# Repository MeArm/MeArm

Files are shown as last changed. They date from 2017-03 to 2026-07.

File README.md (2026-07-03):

MeArm - Pocket Sized Robot Arm 
===========================

4503_additional-mearm-raspberry-pi-transparent-blue-robot-arm_11993340-8186-438d-b66b-95b7427ab5bc_800x

The MeArm is a small robot arm, designed make robotics and coding available at low cost. The project has been hugely successful in its objectives, due to the massive number of clones that have been made and sold across the world. There isn't an online market place where you can't buy a copy of this project. We continue to support the product through income made from the sale of high quality robot kits, manufactured and shipped from the UK.

[MeArm Website](https://www.mearm.com/) Where kits are available to purchase.

[MeArm GitHub](https://github.com/MeArm) Code and resources.

[phenoptix Thingiverse](https://www.thingiverse.com/phenoptix/designs) Physical designs and dxf files, alternative hosting, and other designed products.

Controllers and firmware for the MeArm are available for many different platforms, and can all be found in our [company github](https://github.com/MeArm).

## Available Controllers

Arduino
  - [Library with Inverse Kinematics](https://github.com/MeArm/MeArm-Arduino)
  - pcb V1.0 - AKA Brains Board using Pro Mini Clone
  - pcb V2.0 - AKA MeArm Wifi using ESP8266

Raspberry Pi
  - [node.js control](https://github.com/MeArm/mearm-js)
  - pcb V1.0 MeArm Pi

micro:bit 
  - [pxt adds blocks to makecode](https://github.com/MeArm/pxt-microbit-mearm)
  - [makecode hosted on microbit.org](https://makecode.microbit.org/22476-86653-83739-82174)
  - pcb all versions AKA MeArm micro:bit 

BeagleBoneBlack -[ Software hosted by Bob Stone](https://github.com/RorschachUK/meArmBBB)

Espruino - [JS Hardware with MeArm Examples](https://www.espruino.com/MeArm)

SparkCore - [Software with features such as S-Curve movements
](https://github.com/Hack-a-Day/Spark-MeArm)

Repository Contents
-------------------
This repository contains the design and cutting files for the MeArm. The MeArm is an Open Source 4DOF robot arm. It is intended to be a low cost and accessible robotics project for STEAM education.

Laser cut (3mm) dxf files and Assembly instruction pdf files are sorted into folders based on versions.

Files are collected from the various sources listed above.

## Watch the Build Video on YouTube

<a href="https://www.youtube.com/watch?v=eFOgFglWql4">youtube-thumb</a>

Version History
---------------

Available in this repository

* V3.0 Revised with no elastic bands, still requires a PCB. Build time around 40 minutes.
* V2.0 Designed for MeArm Pi Kickstarter, incorporates a PCB in the base. Requires elastic bands or nitrile O rings. Build time 30 minutes.
* V1.0 First finished version. No PCB required. Build time around 2 hours.

All hosted on Thingiverse .

* V1.0 ([First Finished Version](http://www.thingiverse.com/thing:993759))
* V0.4 ([Considered the Beta Arm](http://www.thingiverse.com/thing:360108))
* V0.3 ([Considered the Alpha Arm](http://www.thingiverse.com/thing:298820))
* V0.2 ([Heavy Weight Revision](http://www.thingiverse.com/thing:293707))
* V0.1 ([Proof of Concept](http://www.thingiverse.com/thing:257990))

License Information
-------------------
The hardware is released under [Creative Commons Share-alike 3.0](http://creativecommons.org/licenses/by-sa/3.0/).  
All other code is open source so please feel free to do anything you want with it; you buy me a beer if you use this and we meet someday ([Beerware license](http://en.wikipedia.org/wiki/Beerware)).
Also this boiler plate is yoinked from Sparkfun with thanks. Images are CC-SA-NC soz, have the files and design but take your own pics ;)

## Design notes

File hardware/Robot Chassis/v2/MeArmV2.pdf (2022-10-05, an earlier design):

Place the base PCB face up (the word TOP should be up) then insert the servo with the double ended arm (there's only one of these) into the hole in the centre. It needs to go the right way around so align the servo arm with the circle on the board

## Read this first!

The MeArm is designed to be easily built with a hex key and some enthusiasm. Here are some tips for a successful build:
Don’t overtighten! The
joints should move freely. If there’s any friction then
loosen off the screws.
Don’t force parts! If a part doesn’t seem to fit, don’t force it, it might just need to be flipped around.

For more detailed video
instructions visit:
http://learn.mime.co.uk/mearm

Slide the centre piece (part #1) down over the servo. The tabs are sized so it will only go on one way round. Wind the servo cable around the centre piece in a clockwise direction through the two holes and then plug it in to the pins as shown

Slide the end pieces (parts #2) down over the centre piece so that they slot into the base. Again, these will only go on one way around

Slide the left side (part #3) over the pins in the base

Slide the right side
(part #4) over the
pins in the base. Loop
one of the elastic
bands around the base
in the upper set of
slots in the sides.
Put this assembly to
one side

Slide the
crossbrace (part
#10) into the left

main strut (part
#5) and click it

in to place

Attach the left rear
strut (part #7) to
the rear of the long
strut you just added
using a 6m screw. It
should go on the
same side as the
main strut

Put the two short
lower levers (parts #8
and #9) together so
that the larger hole
is facing to the
outside, then attach
this to the rear strut
you just added using a
10mm screw through the
hole at the thin end

Clip on the right main
strut (part #11) to the
crossbrace

Screw the rear
strut to the
base using a 6mm
screw

#1

Take the base you
previously built and
screw the arm piece on to
the centre piece of the
base using a 6mm screw.
The screw should go
through the lower lever
and screw into the centre
piece of the base

Slide the right servo in
to place so the servo
arm slots into the hole.
Attach a servo clip
(part #14) to either
side of the servo and
clip it in to the bottom
of the base. Wind the
cable anticlockwise
around the servo clips
and then plug it into
the pins on the base
with the yellow wire to
the right

Slide the right servo in to place and clip it on in the same way. Wind the cable
anticlockwise around the servo clips and then plug it into the pins on the base with the yellow wire to the right.
Place an elastic band around the base and servo clips.

Attach the long strut
(part #6) to the top
of the previous part
using a 10mm screw.
The screw should go
through and hold the
crossbrace in place

# Instructions

#1 | #2 | #3 | #4

Put a 10mm
screw through the
thicker end of part #13
and then through the
triangular piece (part
#12). This piece should

be aligned so that the
screw goes through the
hole marked with a small
triangle and the “m” is
upright

Attach the
upper strut (part
#7) to the upper hole

of the triangular piece
using a 6mm screw

Attach the
right rear strut
(part #7) to the rear
hole on the triangular
piece using a 6mm screw

Put this assembly to one side for a moment

# Continue on the other side >

#5 | #6 | #7 | #8

#9 | #10 | #11 | #12 | #13

#14 | #15 | #16 | #17

MeArm Pi Instructions | MeArm WiFi Instructions

# MeArm Maker Instructions

Take the remaining servo and align the arm as shown in the picture. Take the left grip side (part #15) and slide it on to the end of the servo closest to the arm

Slot the centre grip support (part #16) on to the other end of the servo facing the same way as the other end

Clip the grip front plate (part #17) on to the front of the two pieces you slotted on to the servo. It should clip up into place. Make sure the extra hole is at the opposite end to the servo arm

Slot the left grip side (part #18) in to the third hole in the front plate

Slide the rear grip support (part #19) in to the gap and turn it up so it slots into place. The lower edge of it should be level with the front plate

Take the left grip (part #20) and place it over the servo arm. Align the right grip (part #21) with the left and hold in place

#26a Align the two

large base pieces
as shown. Screw
them together
using four 6mm
screws. Do not
overtighten the
screws

#26b Stretch the

elastic bands
over the sides of
the base to use
as feet

Gently prise the two base plates apart and slide the servo arm in between them and slide it down the central slot until it clips into place in the hole in the bottom

Slide the grip base
(part #22) on so
that the large hole
aligns with the
servo arm side and
screw it into place
through the right
grip with a 10mm
screw

Before starting this part set up your SD card. Instructions at: http://learn.mime.co.uk/mearm

Attach the grip to the rest of the arm using three 6mm screws. Tuck the cable down through the slot on the grip, then in and out of the
crossbrace on the arm,
plugging it in to the pins on the base with the yellow wire on the right.
Now choose one of the
following three steps to
continue

Attach the final
elastic band across
the front of the
base to hold the
plates together and
make a stable foot
to stand it on

Plug the two parts
together using the
ribbon cable provided

## Congratulations!

You’ve just built a robot arm!

Plug in the power supply to get it working and visit: http://learn.mime.co.uk/mearm
to begin using and programming your MeArm

If you have any problems you can get help at: http://mime.co.uk/support

#26a Align the two

large base pieces as
shown. Plug the HAT
on to the GPIO pins
of the Raspberry Pi.
One by one, slot a
spacer in between the
Pi and HAT then slot a
16mm screw through to hold it in place. Screw all four screws into the holes in the base

#26a Align the two

large base pieces
as shown. Slot the
small round spacers
under the PCB then
screw in a 10mm screw
to hold it in place

Do not overtighten the screws

#26c Fit the cover

over the tabs on the
sides and stretch an
elastic band over each
side. Push the joystick
caps on to the joysticks,
making sure they are properly aligned before pushing

#26c Fit the

cover over the
tabs on the sides
and stretch an
elastic band over
each side. Push the
joystick caps on to the
joysticks, making sure they are properly aligned before pushing

#26b Slot the front (part #24) and back (part #23 or #25

for the Pi Zero) edges
into place. Slot part
#25 into place on the

left of the base plus
one on the right if
you're using a Pi Zero

#26b Slot the front (part

#24) and back (part #23)

edges into place. Slot
parts #25 into
place on the
right and left of
the base
#18 | #19 | #20 | #21 | #22 | #23

#24 | #25

#27 | #29

#28

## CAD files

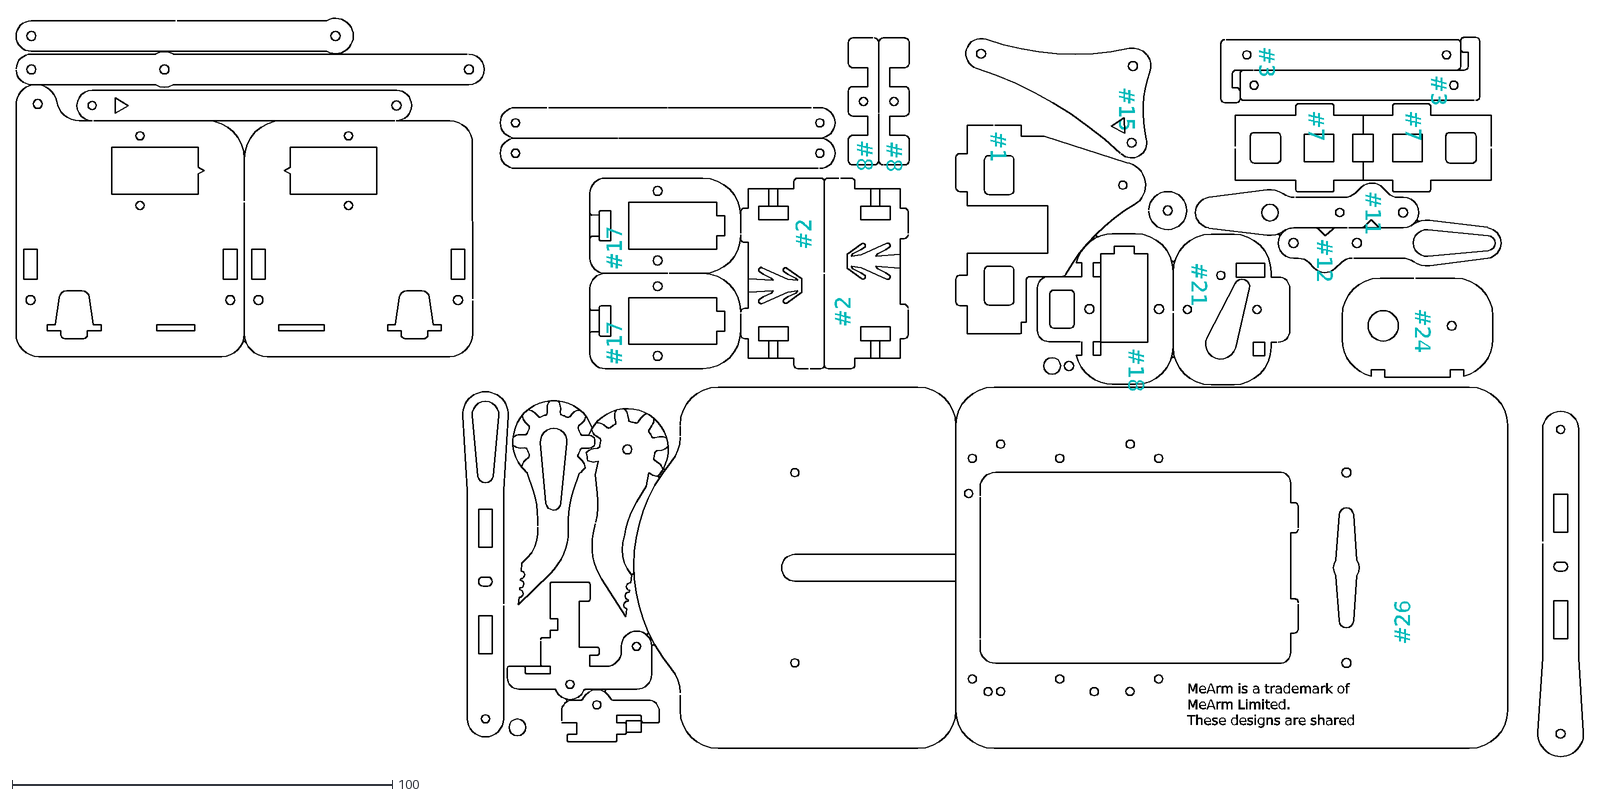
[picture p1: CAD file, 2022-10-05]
hardware/Robot Chassis/v3/MeArmV3.dxf
#26
#1
#3
#7
#8
#11
#12
#15
#18
#21
#24
#2
#17
MeArm is a trademark of
MeArm Limited.
These designs are shared

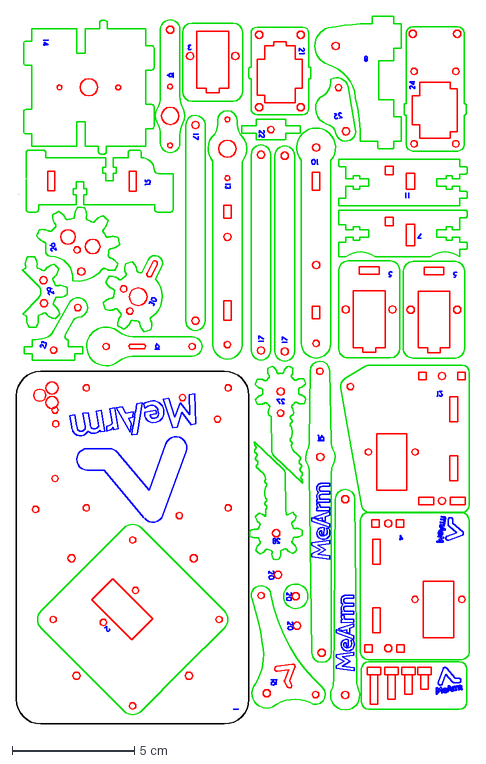
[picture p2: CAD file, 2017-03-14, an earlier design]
hardware/Robot Chassis/v1/MeArmV1.1.dxf
18.5 x 28.9 cm

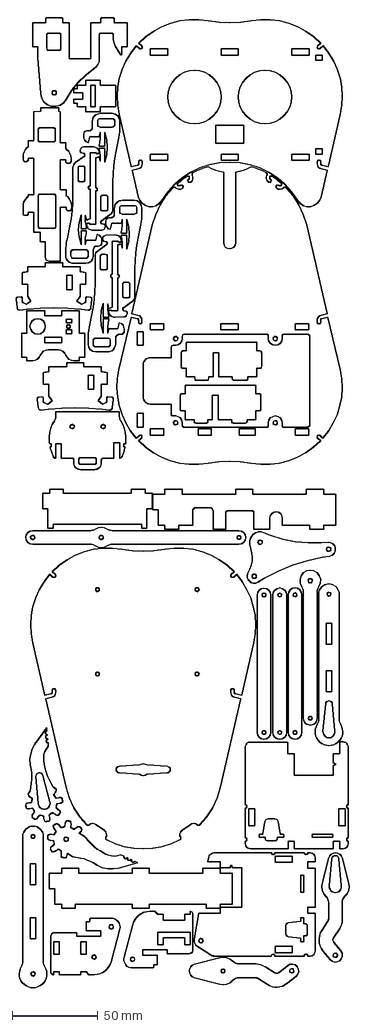
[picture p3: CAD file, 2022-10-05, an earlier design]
hardware/Robot Chassis/v2/MeArmV2.dxf
194.2 x 565.6 mm

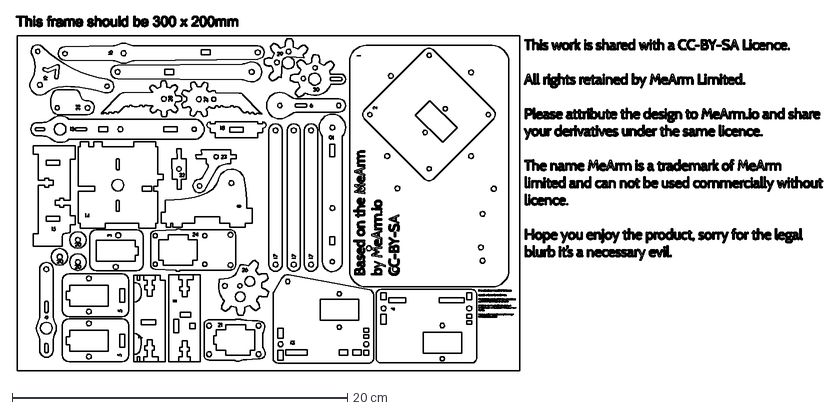
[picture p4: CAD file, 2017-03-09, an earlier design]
hardware/Robot Chassis/v1/MeArmV1.0.dxf
48.1 x 21.2 cm

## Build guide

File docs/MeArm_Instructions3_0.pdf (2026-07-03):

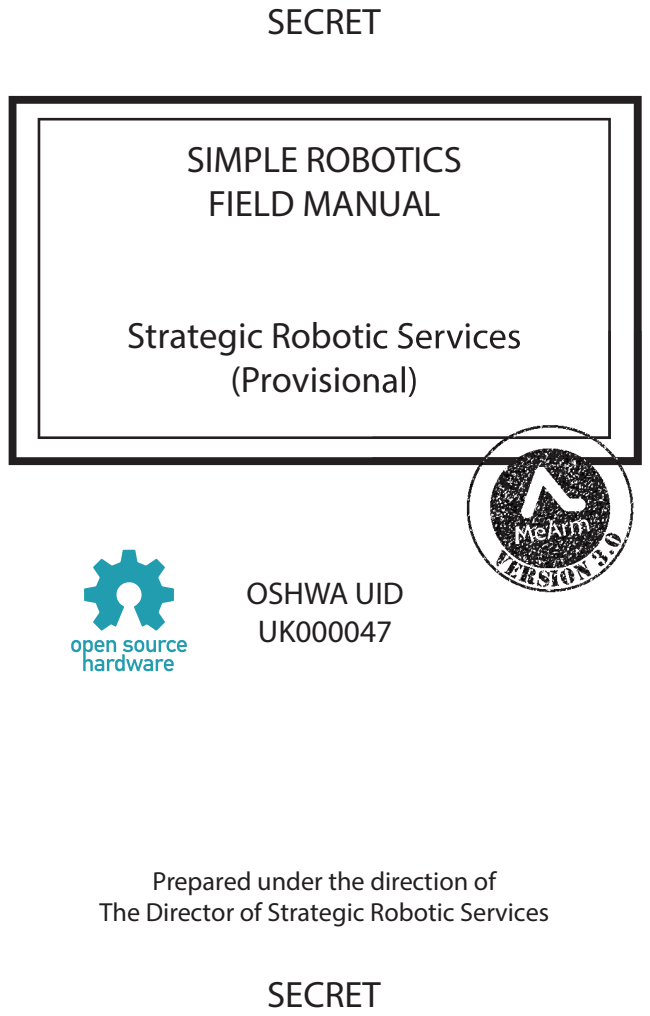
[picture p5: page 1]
SIMPLE ROBOTICS FIELD MANUAL; SECRET; OSHWA UID UK000047

Strategic Robotic Services
(Provisional)

Prepared under the direction of
The Director of Strategic Robotic Services

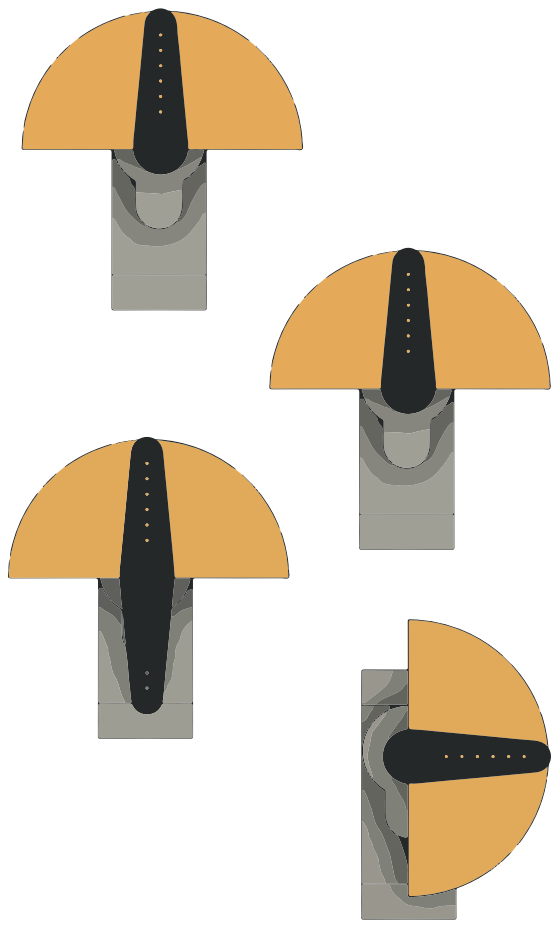
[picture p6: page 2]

Important Notes:

Before assembly you will need to test and calibrate your servo motors to the positions shown overleaf.

The process differs depending on your choice of control board. Please head to https://shop.mearm.com/build and select the correct product.

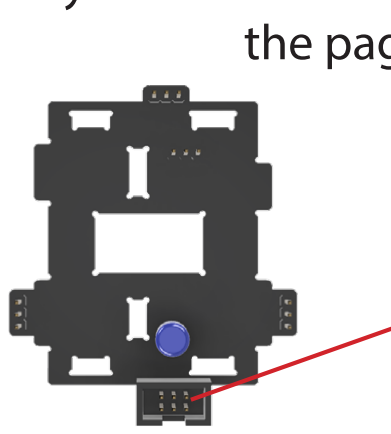
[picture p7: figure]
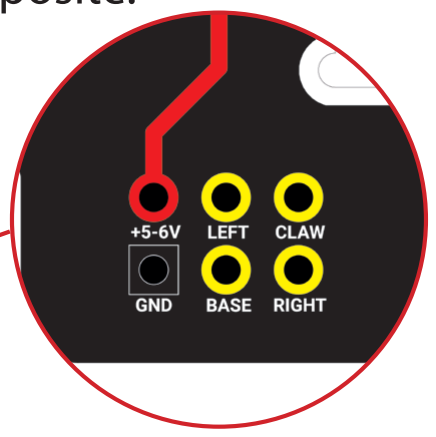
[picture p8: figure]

If you do not calibrate your servo motors now you will need to dismantle parts of your MeArm later on.

Do not skip ahead. Calibrate your servos so they are able to move in the arcs shown on the page opposite.

The MeArm project started in 2014, with the aim of making a robot arm that was made from a small number of components, was easy to assemble, and fun to use. The design files were shared online and the first viral robot arm was born. This latest version is the product of thousands of hours of open source development, from all around the globe.

We hope you will enjoy the product you have purchased, and we thank you for your support and feedback.

Remember:
- Joints should move freely. Without the servo motors fitted the robot should be a like a resting marionette.
- Parts should sit in place with very little or no force. It may be that you can rotate a part to get it to fit.

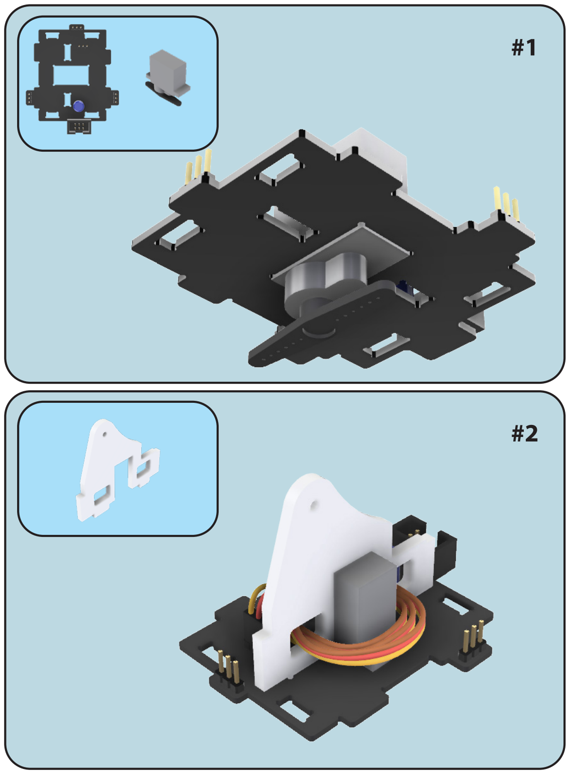
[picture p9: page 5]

#1

#2

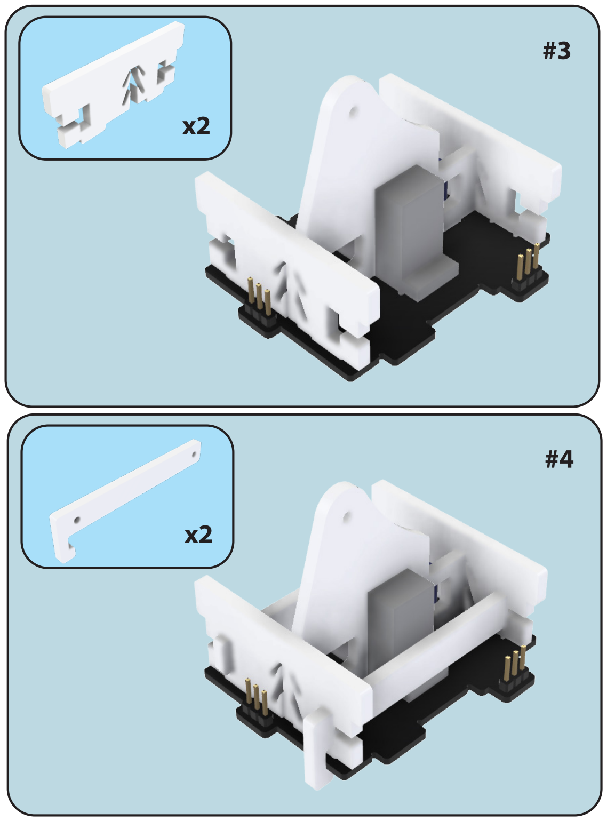
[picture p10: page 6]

#3

x2

#4

x2

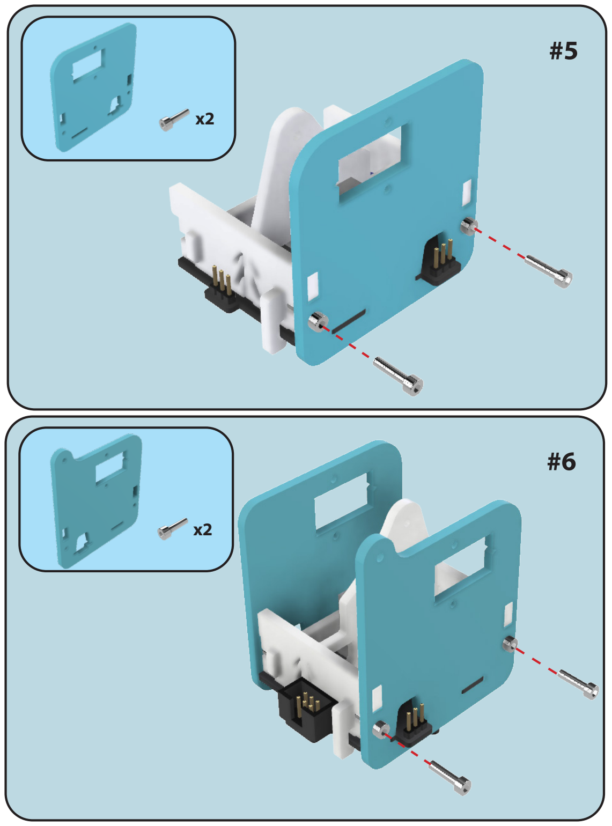
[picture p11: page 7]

#5

x2

#6

x2

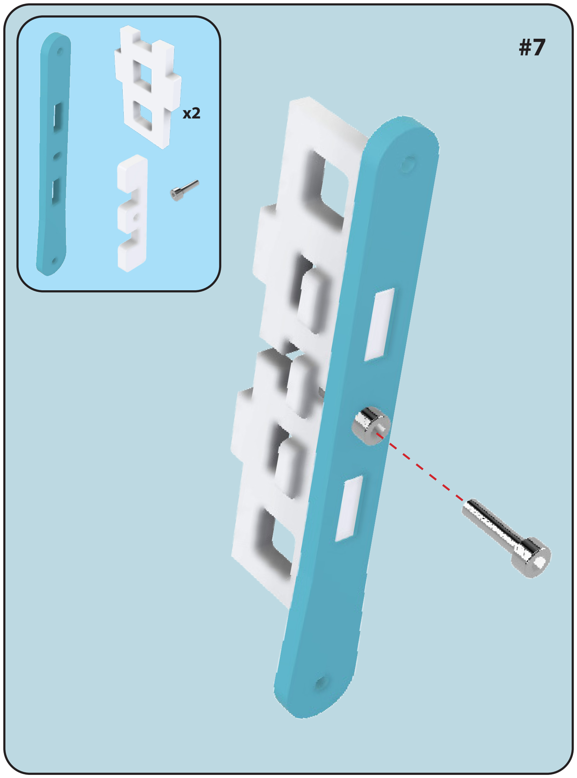
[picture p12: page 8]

#7

x2

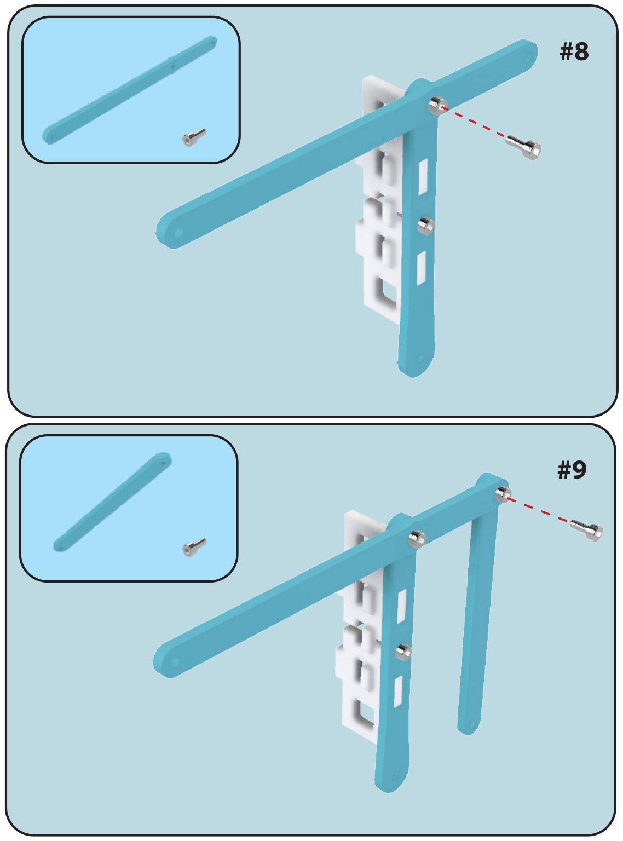
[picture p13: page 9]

#8

#9

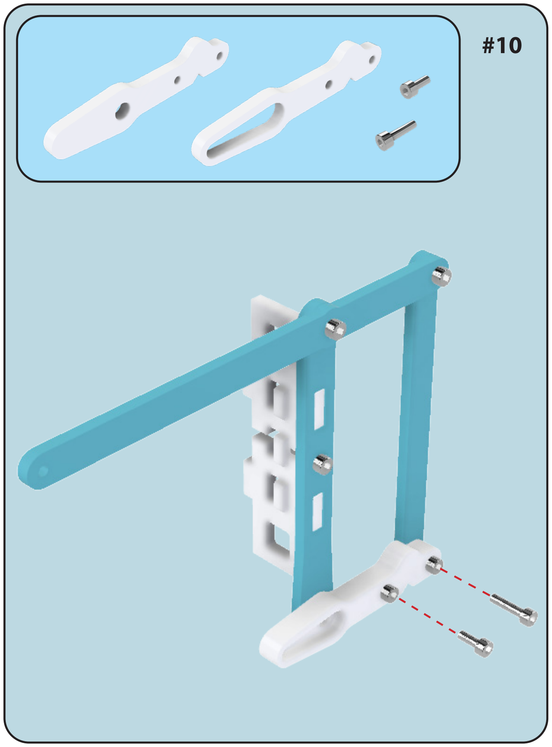
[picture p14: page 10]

#10

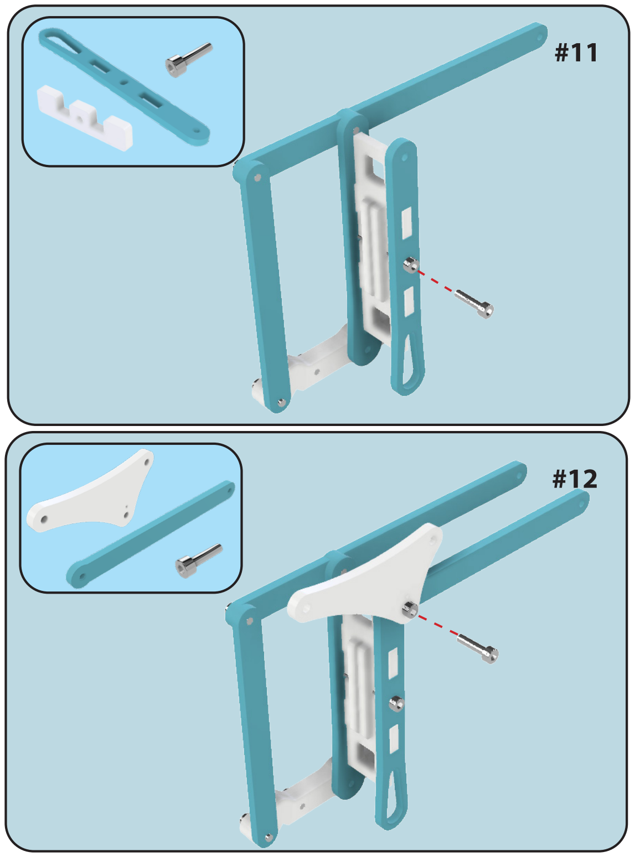
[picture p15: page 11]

#11

#12

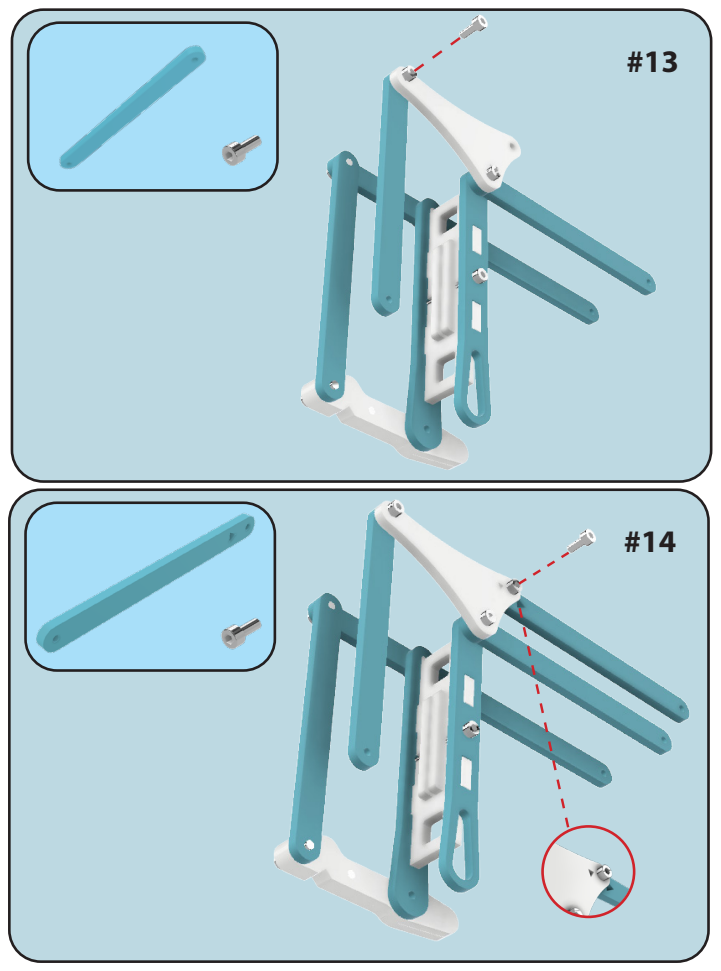
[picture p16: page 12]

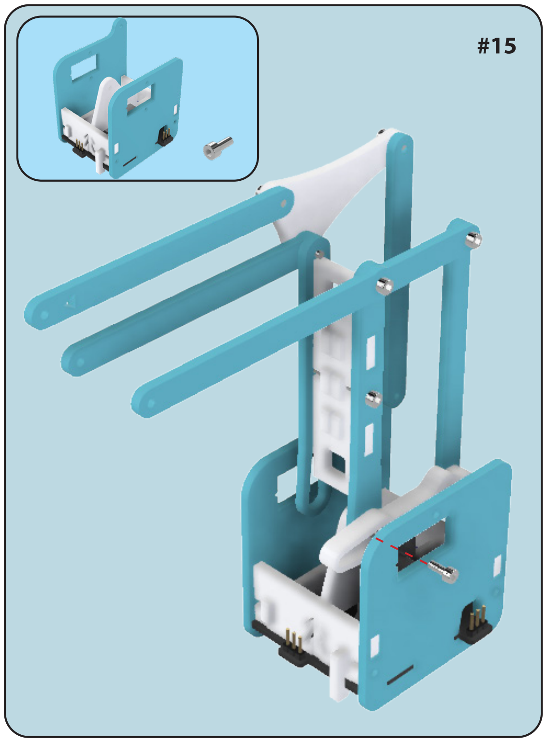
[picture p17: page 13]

#15

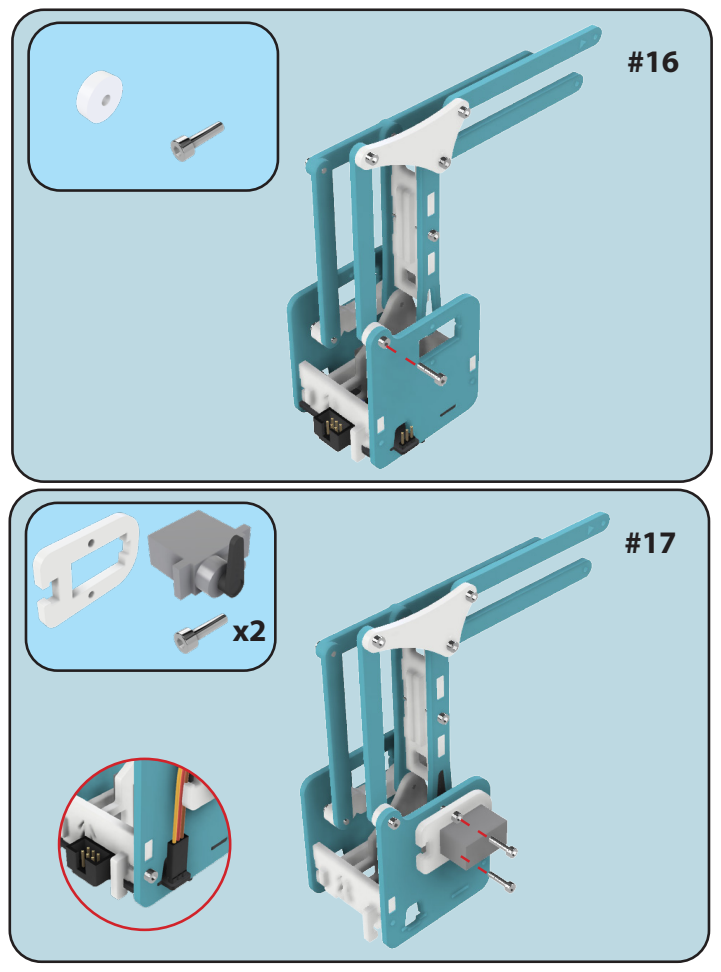
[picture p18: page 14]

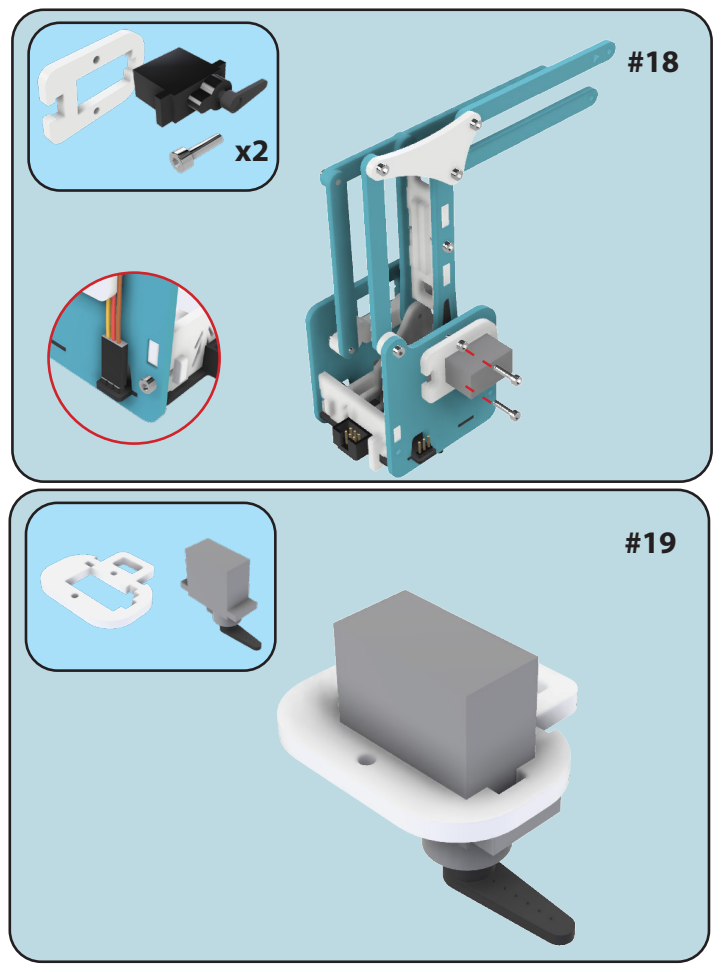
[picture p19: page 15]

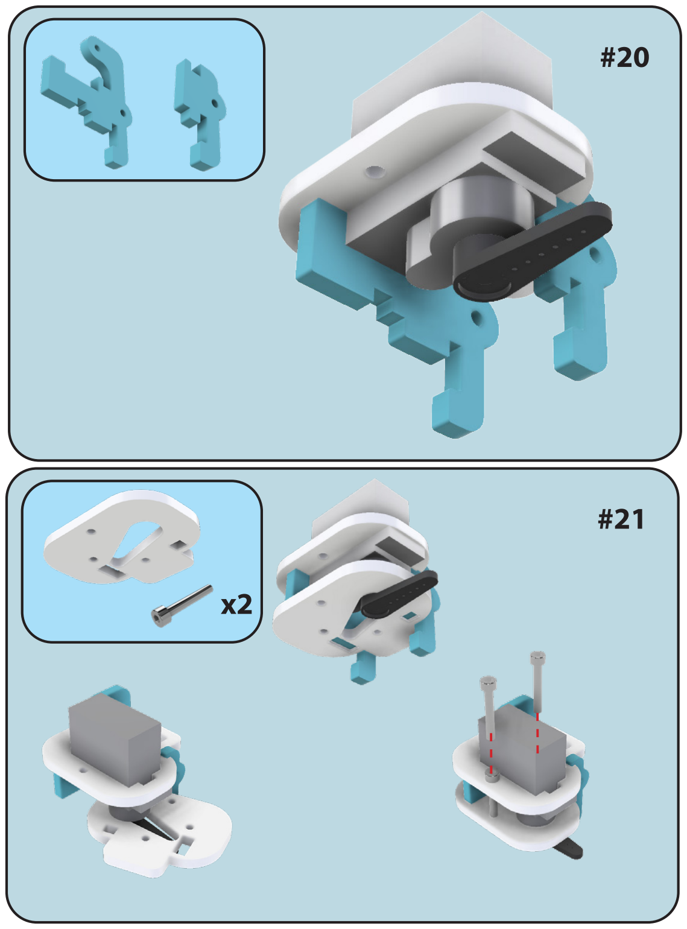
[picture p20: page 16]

#20

#21

x2

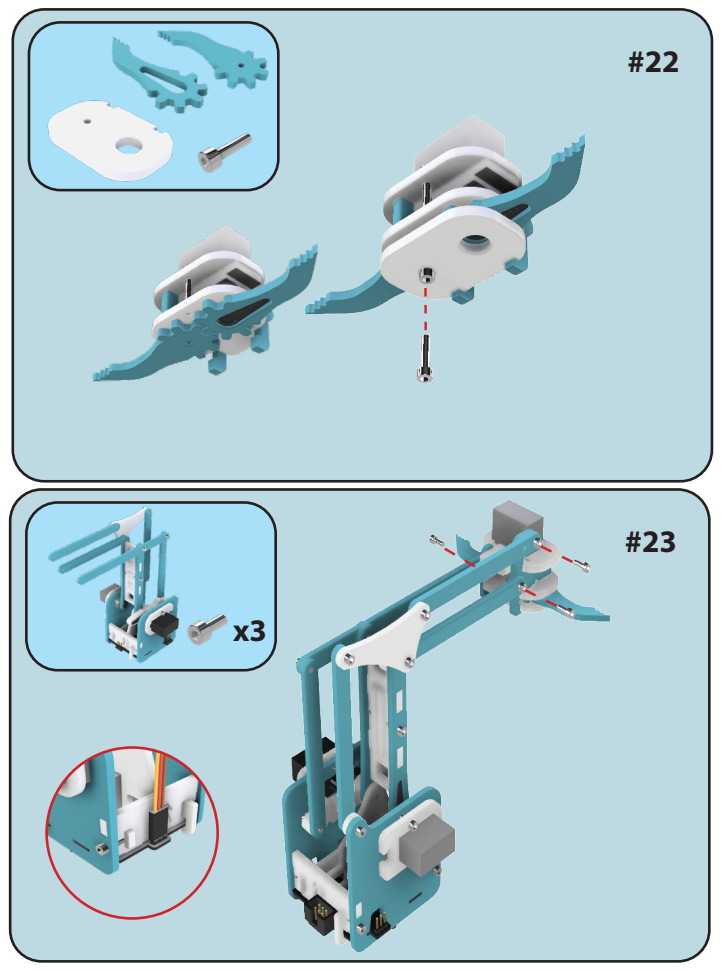
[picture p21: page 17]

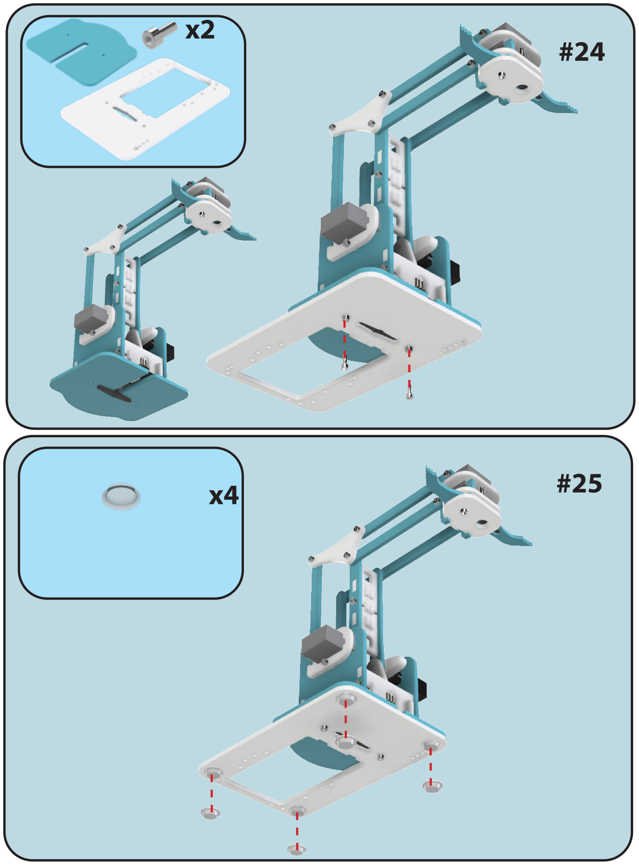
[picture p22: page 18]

#24

x2

#25 x4

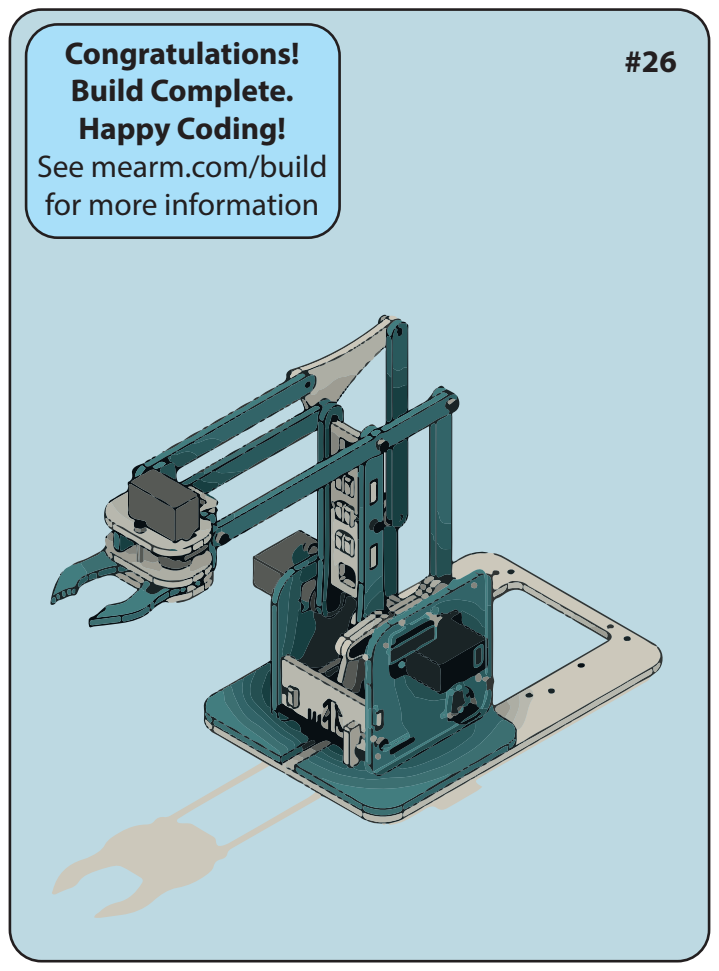
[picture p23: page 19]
Congratulations!

Build Complete.
Happy Coding!
See mearm.com/build
for more information

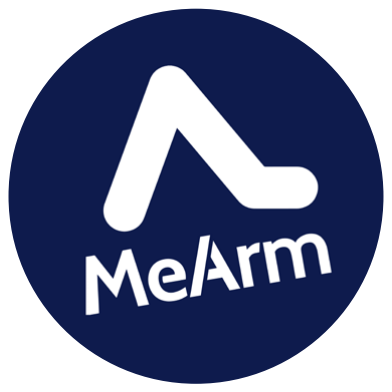
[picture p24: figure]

Thank you for buying this geniune MeArm product.

You can find us on most social media platforms at MeArmTM and our websites at www.mearm.com and www.mime.co.uk

© MeArm Robotics and Mime Industries 2023, All Rights Reserved

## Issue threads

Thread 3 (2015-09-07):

IK Question

Scott216, 2015-09-07:
I don't have this arm, but I do have a 4-axis arm from Sain Smart which is somewhat similar. My question is, when you move the servo that adjusts the angle between horizontal and bicep (abi), does the angle between the bicep and forearm change, even if you are not moving that servo?
I'm trying to figure out the kinematics for my arm, but it's hard because if I change abi angle, the afo angle also changes just by the way the arm is designed.  So if I want the afo angle to remain the same, I actually need to move that servo that controls the afo angle as the abi angle changes. I haven't been able to figure out how to do that yet?

mithi, 2015-09-08:
In my version of the MeArm (also a derivative), the two axes are
independent. I know this because when when I hold one link so that it
resists the movement caused by the other arm, it can independently move
only up and down or forward and backward with out affecting the other. This
is directly because of the measurement of the 4 bar linkages in which the
arm is based. Check if your Saint Smart arm has the same measurements as
the one of the original meArm. I think there is a youtube video (an Indian
guy) which discusses this concept, you might want to search for it. I'll
try to post some pictures later to further illustrate the concept :)

http://mithi.xyz

On Mon, Sep 7, 2015 at 8:13 AM, Scott Goldthwaite <notifications@github.com>
wrote:

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

mithi, 2015-09-08:
Sorry my bad scratch this comment I was talking about a different arm.

On Tue, Sep 8, 2015 at 9:24 AM, Mithi Sevilla <mithi.sevilla@gmail.com>
wrote:

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

mithi, 2015-09-08:
Okay here goes the update version of my comment

In my version of the MeArm (also a derivative), the two axes are
independent.
 I know this because when when I hold one link so that it resists the
movement caused by the other link, it can independently move only up and
down or forward and backward with out affecting the other.

*You might mistake that the two axes are dependent because of the following
reasons (I got confused as well initially) *

1. When you change the end effectors position without constraining the
motion of one link, then both servos will move, but this due to the natural
forces acting on them, not because they are dependent. Think of it like a
frictionless pivot vs a pivot with friction.

2. The shape of the parallelogram of each four-bar linkage which each servo
controls changes when you rotate each axes independently even when
constraining  the movement of the other servo. This does not mean they're
the angle of the servo with respect to the "world/fixed frame" or the
horizontal does not change. Try to ignore the four bar linkage and picture
only the link which the servo is directly connected to reinforce this
concept in your mind.

I will post a short video to aid this comment later :)

By the way however if you move it directly horizontal, naturally the the
two independent angles change ( as dictated by the inverse kinematics).
(which means if I constraint one link from moving, and i move the
end-effector directly forward or backward I will feel a resistance tugging
me and wont be able to reach my goal. Careful! Don't force it or your arm
might break!)

I hope I answered your question well :)

http://mithi.xyz

On Tue, Sep 8, 2015 at 9:26 AM, Mithi Sevilla <mithi.sevilla@gmail.com>
wrote:

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
>>> I don't have this arm, but I do have a 4-axis arm from Sain Smart which
>>> is somewhat similar. My question is, when you move the servo that adjusts
>>> the angle between horizontal and bicep (abi), does the angle between the
>>> bicep and forearm change, even if you are not moving that servo?
>>>
>>> I'm trying to figure out the kinematics for my arm, but it's hard
>>> because if I change abi angle, the afo angle also changes just by the way
>>> the arm is designed. So if I want the afo angle to remain the same, I
>>> actually need to move that servo that controls the afo angle as the abi
>>> angle changes. I haven't been able to figure out how to do that yet?
>>>
>>> —
>>> Reply to this email directly or view it on GitHub
>>> <https://github.com/phenoptix/MeArm/issues/3>.
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

Scott216, 2015-09-09:
Hi Mithi,
I think your arm works similar to mine.  Thank you for the videos.  At the start of your video (https://youtu.be/1Q3unEnOJ0E?t=0s), you are holding one servo stationary.  But as you move the arm  the angle between horizontal and the bicep arm change as does the angle between the bicep and forearm.  In the IK formulas I've seen like this one: http://www.oliverjenkins.com/blog/2012/9/inverse-kinematics-and-robot-arms, if you only move one servo, then only that angle changes.  In your arm and my arm, if tell the servo for θ1 to move, θ2 angle will also change even if that servo hasn't changed because the servo is not located at the joint between the bicep (L1) and forearm (L2).
For example, on my arm, if I start out with  θ1 at 90 degrees and  θ2 also at no degrees.  Then I have the bicep servo move about 45 degrees so the arm moves forward and I tell the forearm servo not to move at all, then the  θ1 angle about 45, but  θ2 is approximately 135 degrees. The IK formulas I've seen assume  θ2 is still at 90 degrees in this example.
I did a little experimenting and figured out for every degree I move the bicep servo, I need to move the forearm servo at the same time by 1.2 degree if I want to keep θ2 from changing, but this doesn't work for the whole range of motion of the arm.
What IK formulas are you using for your arm?

mithi, 2015-09-09:
I see what you mean. It's because it's a parallel four-bar linkage.

I didn't really do the inverse kinematics yet, but maybe this quick sketch
might help you.

[image: Inline image 2]

The geometrical relationships from the diagram
*180 = theta2 + (180 - theta1) + theta*
*simplifying you get *
*theta1 = theta2 + theta *

Example

*first position *
theta1 = 90 angle of link1 wrt to the horizontal
theta2 = 45 angle of link 2 wrt to the horizontal
theta = 45 angle between link1 and 2

*2nd position *
we move theta one 45 degrees counter clockwise, as a result:

theta1 = 135 angle of link1 wrt to the horizontal
theta2 = 45 angle of link 2 wrt to the horizontal
theta = 90 angle between link1 and 2

I hope I answered you question.

On Wed, Sep 9, 2015 at 11:04 AM, Scott Goldthwaite <notifications@github.com
> wrote:

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

Scott216, 2015-09-09:
Thanks.  I actually just did a similar sketch and it really helped to understand the relationship between the angles.  It turned out to be simpler then I thought.  We'll see if I can get the IK working properly

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

mithi, 2015-09-09:
Have you seen  a few  implementations?
https://github.com/phenoptix/me-arm-ik
also
https://github.com/phenoptix/meArm-1

among a few others.

I haven't gotten around to look at it in detail yet. But it looks pretty straight forward and the authors gave comments generously

Scott216, 2015-09-09:
Thanks for the links, I'll check them out.

Closed 2017-03-09.

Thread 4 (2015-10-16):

Question regarding the movement of the IK example

CaptainMack, 2015-10-16:
Hi guys!

I just built mine own MeArm and I've tried the IK example from this repository, however as the code says that the
    arm.gotoPoint(-80,100,140);

should go up and left, but it goes down and to the left - one of the servos are doing the opposite. However, the next step (for going down, forward and right) says:

```
arm.gotoPoint(70,200,10)
```

but the y-axis is second parameter, shouldn't it be going up? as in fact is happening and contrary to what's mentioned in the inline comments? Or did I miss something? (Probably the case!)

Thanks for an awesome opensource project!

Closed 2017-03-09.

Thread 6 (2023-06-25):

MeArmプロジェクトへの貢献

zuhiro, 2023-06-25:
Hi, I'm ZUHIRO.

I would like to thank you for publishing MeArm on Github.

I was impressed with MeArm and I was thinking about something that I could do, so I am making a new robot arm based on the data of the MeArm project.

I named it "eleArm".

eleArm aims to simplify the assembly by reducing the number of parts compared to the conventional MeArm.

Raspberry Pi pico is used for control.

I am thinking of publishing eleArm on Github as Open Hardware after it is completed.

My goal is to have eleArm ready for workshops for children.

I am a beginner in OSS activities and I have a lot of things I do not know.

If there is any problem with MeArm's activities, please let me know.

Please let me know if there is anything I can do to help the MeArm project.

[https://photos.app.goo.gl/3669fKdyqvB4Aqij6](url)

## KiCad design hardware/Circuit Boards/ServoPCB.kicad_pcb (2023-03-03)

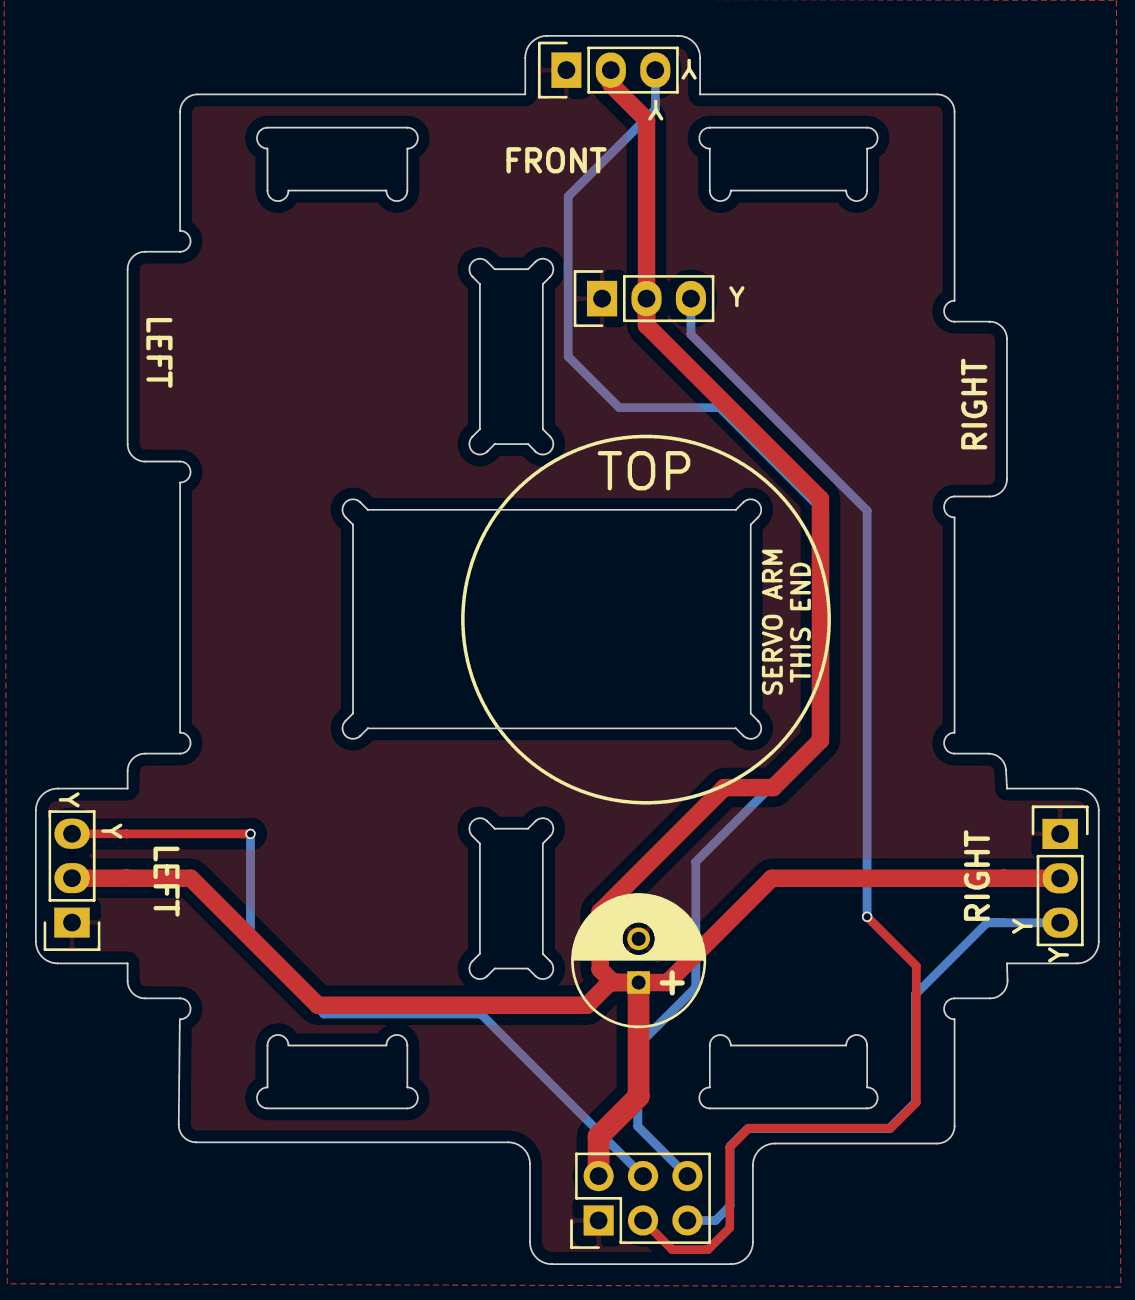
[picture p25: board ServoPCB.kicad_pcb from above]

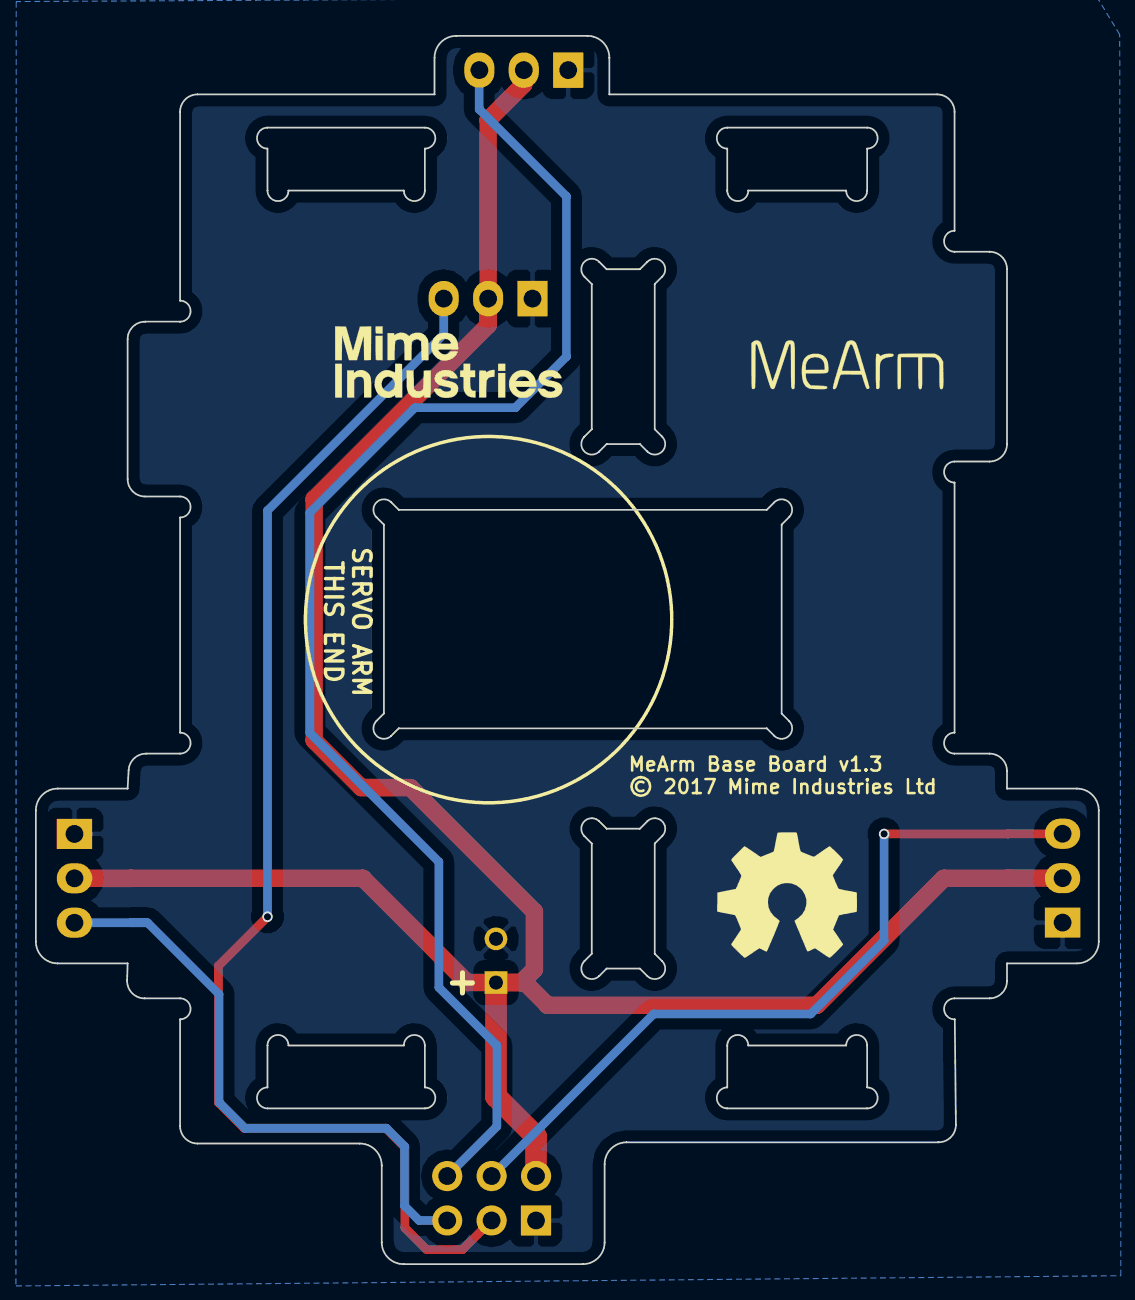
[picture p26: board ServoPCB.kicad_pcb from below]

Board: 2 copper layers, 60.8 x 70.3 mm, 9 parts (3 on the bottom side), 6 nets.

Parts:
ART1: OSHW-LOGO; OSHW_LOGO
ART2: LOGO; MIME_LOGO
ART3: LOGO; MEARM_LOGO_NEW
C1: 470uF; C_Radial_D7.5_L11.2_P2.5
P1: CONNECTOR; Pin_Header_Straight_2x03
P2, P3, P4, P5: Pin_Header_Straight_1x03

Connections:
GND: C1.2, P1.1, P2.1, P3.1, P4.1, P5.1
unnamed: P1.3, P2.3
unnamed: P1.4, P3.3
unnamed: P1.5, P4.3
unnamed: P1.6, P5.3
VCC: C1.1, P1.2, P2.2, P3.2, P4.2, P5.2

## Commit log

2014-04-23 Arduino Code for MeArm
    Control with 10k Pots
2014-05-01 Typo in pin numbering comments
2014-05-07 Inverse Kinematics in the XZ plane
    Should be trivial to add it to the XY too. Still uses 10k pots for
    input. Out of time for today.
2014-12-17 First Commit
    Upload of KiCAD MeArm Controller Leonardo Files
    [MeARM_Controller_Leonardo.brd, MeARM_Controller_Leonardo.sch]
2015-03-26 New Board Version
    Retired the previous MeBrain board for this Brains board. v2.0 all files
    available for your delectation.
    [MeARM_Controller_Leonardo.brd, MeARM_Controller_Leonardo.sch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]
2015-09-01 V1.0 Update
    Kickstarter Production version
    [brains-B_Cu.gbl, brains-B_Mask.gbs, brains-B_SilkS.gbo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]
2016-02-26 pdf schematic as requested
2016-11-29 more moving
    [brains.kicad_pcb, brains.sch]
2016-11-29 Add Hardware Folder to MeArm Structure
    Hardware folder to contain all hardware related files, PCB and
    structure.
    [brains.kicad_pcb, brains.sch]
2016-11-29 Moved Arduino Files to Arduino Folder
2016-11-29 Links to code for BBB, Raspberry Pi and Spark Core
2017-03-09 Re-worked to bring in the dxf files, starting with v0.1
    [MeArm.dxf, brains.kicad_pcb, brains.sch]
2017-03-09 Adding v0.2
    [MeArm.dxf]
2017-03-09 Adding v0.3
    [MeArm.dxf]
2017-03-09 Adding v0.4
    [MeArm.dxf]
2017-03-09 Adding v1.0
    [MeArm.dxf]
2017-03-14 Add v1.1 of the MeArm design
    [MeArm.dxf]
2022-10-05 v1 to v3 files collected together
    [MeArm.dxf, MeArmV1.0.dxf, MeArmV1.1.dxf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]
2023-03-03 Detail and essentials
    Filled out readme a little more and added KiCad files for the PCB. Would gerbers be more useful? If anyone is looking and cares please let me know.
    [ServoPCB.kicad_pcb]

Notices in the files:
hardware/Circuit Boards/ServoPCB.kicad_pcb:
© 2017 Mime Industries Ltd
